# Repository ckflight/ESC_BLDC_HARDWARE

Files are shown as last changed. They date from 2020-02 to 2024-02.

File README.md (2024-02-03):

# BLHELI_S Electronic Speed Controller Hardware Design

#### ESC Information:

 * BLDC 3 phase motor speed controller hardware design working with open source BLHeli_S C configuration firmware C_H_30.

 * The ESC is tested on a real quadcopter with brushless motors at 40 Ampere current rating. 
 
 * TPN2R703NL Power MOSFETs are used on this design, which are capable of delivering current up to 45 Ampere for normal operation and 90 Ampere peak for short pulse.
 
 * MP1907 High Frequency Half Bridge Gate driver is used for controlling the Power MOSFETs. High power MOSFET transistors have high Q and capacitance values. To open the gate it requires high amount of current in short amount of time where current requirement decreases exponentially. This is the reason for using a Gate Driver. Also an extra gate resistor is populated at the input of MOSFET gate pin.
 
 $$ Igate(max) = {Vgate \over Rgate} $$

        4S Lipo Battery Vgate = 16V, Rgate = 10 Ohm and Igate(max) = 1.5A
 
 $$ Igate = {Qfet \over Tswitch} $$
 
         For a MOSFET with Qtotal = 50nC Tswtich = 500nS and Igate(needed) = 0.1A.
         Therefore, a 100 Ohm gate resistor is populated.

 * Phase C has current bar trace. Or it can be done with extra solder on the trace.

esc1

esc1

esc2

# BLHELI_S Firmware Flashing Guide

When esc is new assembled the EFM8BB2 does not have BLHeli_S Bootloader.
For the first time flashing, 4wire interface is used by using C2CK, C2D, 3.3v and GND pins where it will load both bootloader and firmware to esc.
After this step, esc can be flashed with 1-Wire interface (Esc's pwm pin).

####Flashing ESC for the first time.

1. Open "Make interfaces" section
2. Select the Arduino board that will be used as programmer.
3. Click "Arduino 4way-interface" and flash it to arduino.
   (Now arduino became a 4wire programmer)

4. Select "SILABS C2 (4way if)"
5. Connect Arduino to Custom ESC
       GND to GND 
       3.3v to 3.3v
       Arduino Pin12 to C2D 
       Arduino Pin11 to C2CK
6. Open ESC Setup section and connect to esc and click Flash BLHeli
   (choose suitable version, my custom quadcopter esc v2 is working with C type)

Now the esc is both flashed with blheli bootloader and the blheli firmware, 
therefore 1wire interface can be used which is the esc's pwm pin. 
Or flight controller can be used in passthrough mode.

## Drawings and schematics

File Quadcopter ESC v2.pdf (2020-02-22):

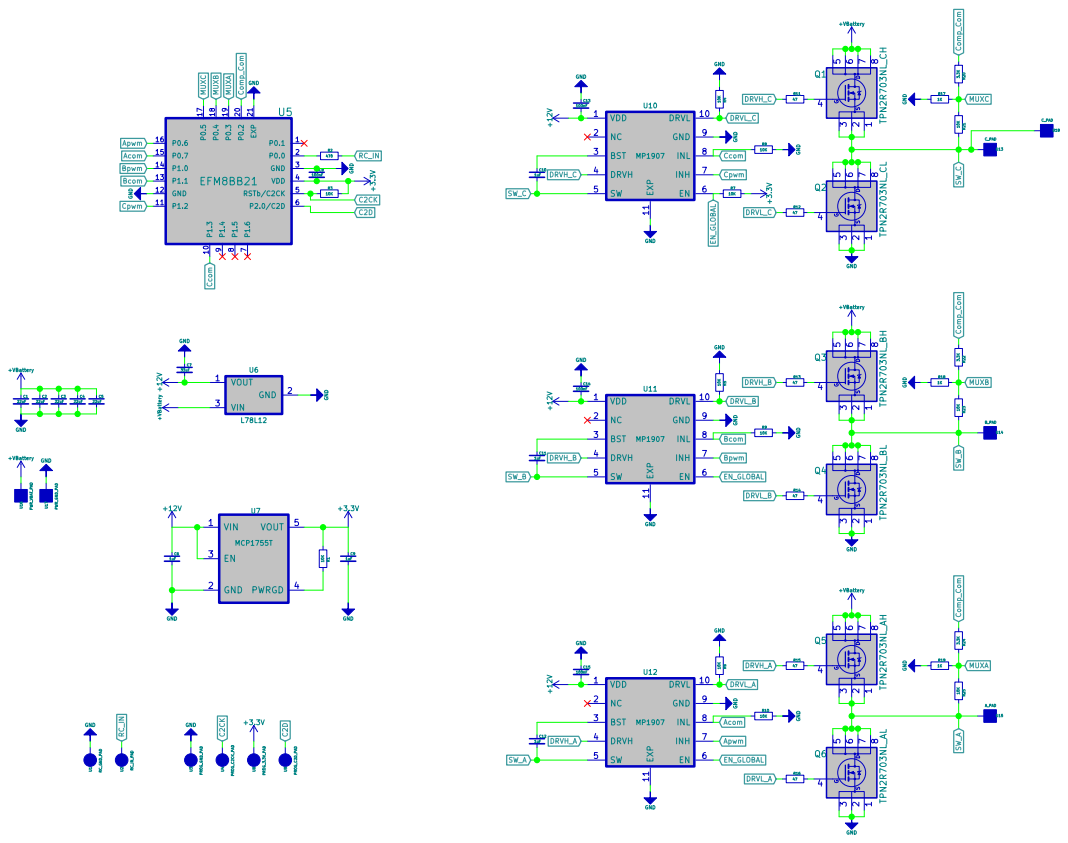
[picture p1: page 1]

File: Quadcopter ESC v2.sch Sheet: /
Id: 1/1 Title: Cenk Keskin

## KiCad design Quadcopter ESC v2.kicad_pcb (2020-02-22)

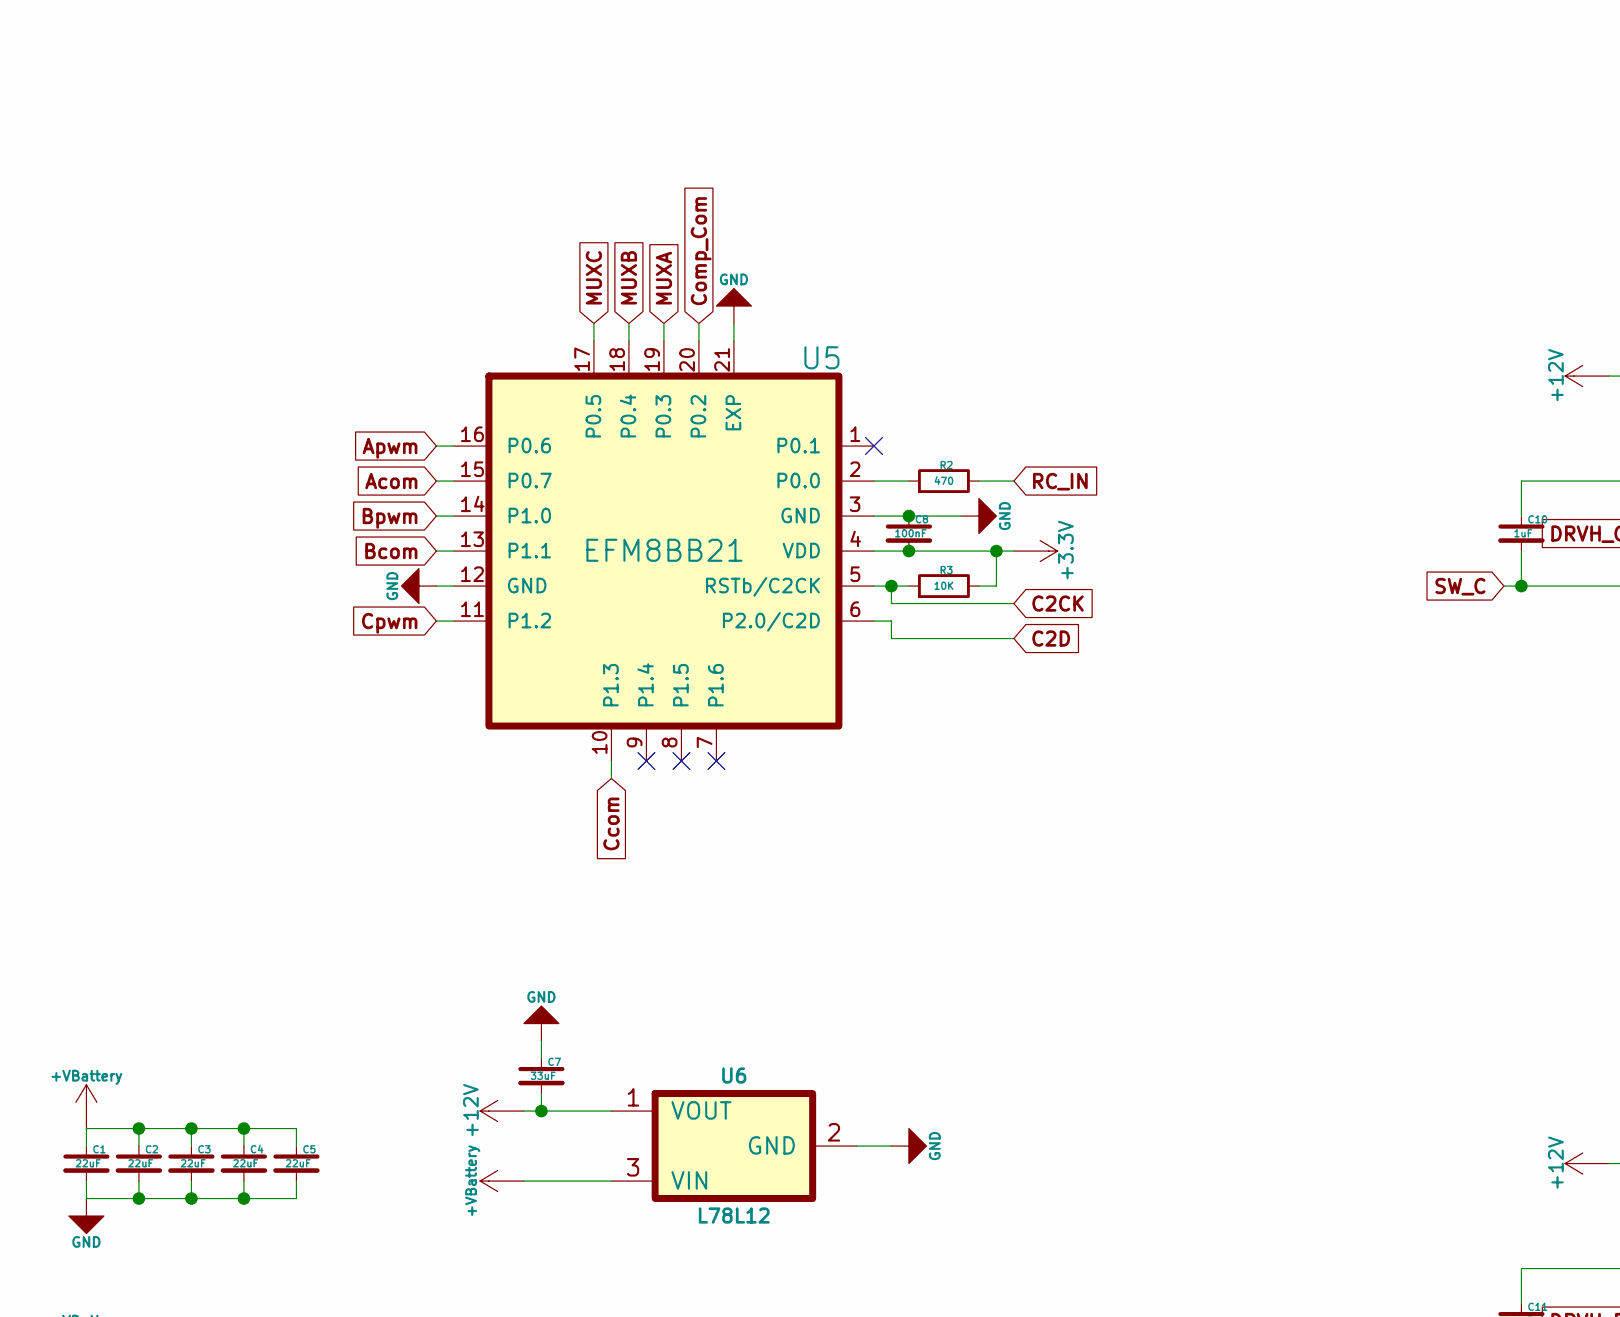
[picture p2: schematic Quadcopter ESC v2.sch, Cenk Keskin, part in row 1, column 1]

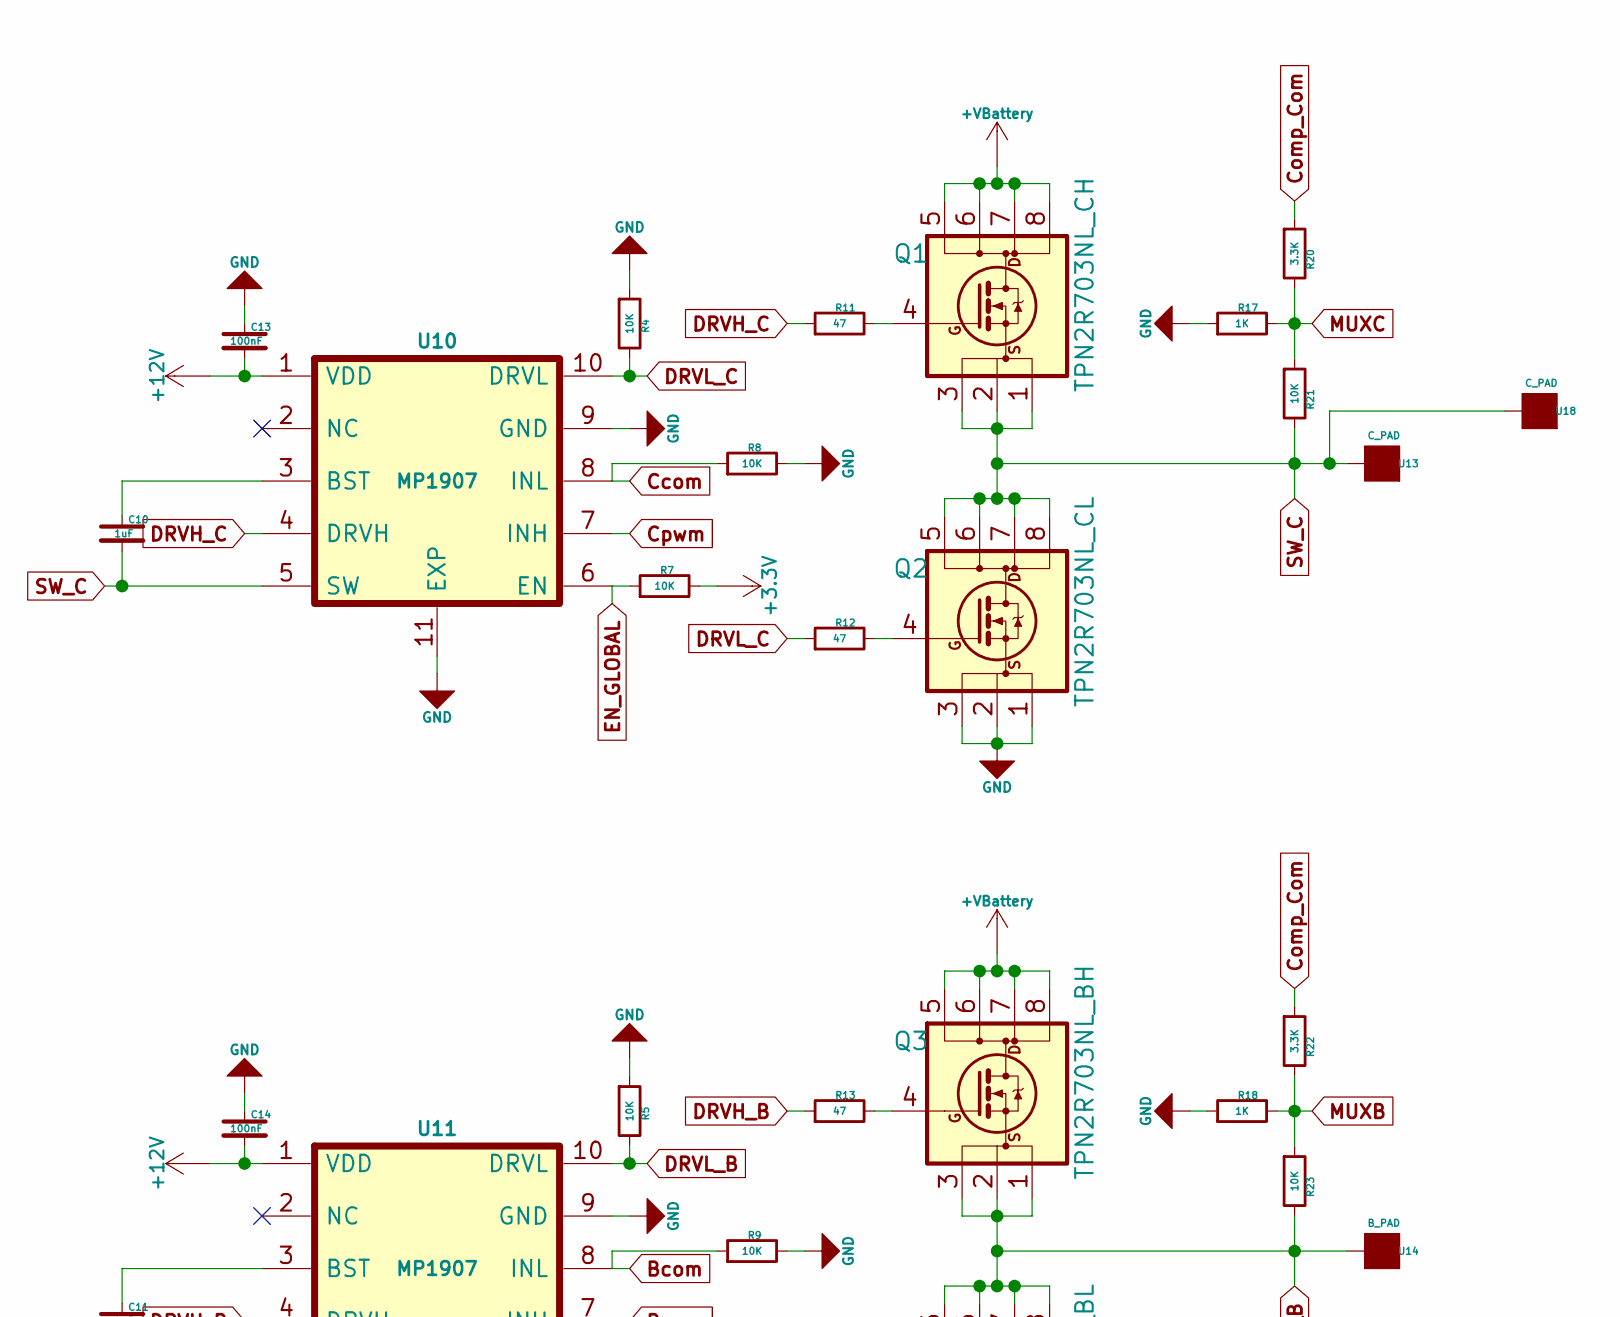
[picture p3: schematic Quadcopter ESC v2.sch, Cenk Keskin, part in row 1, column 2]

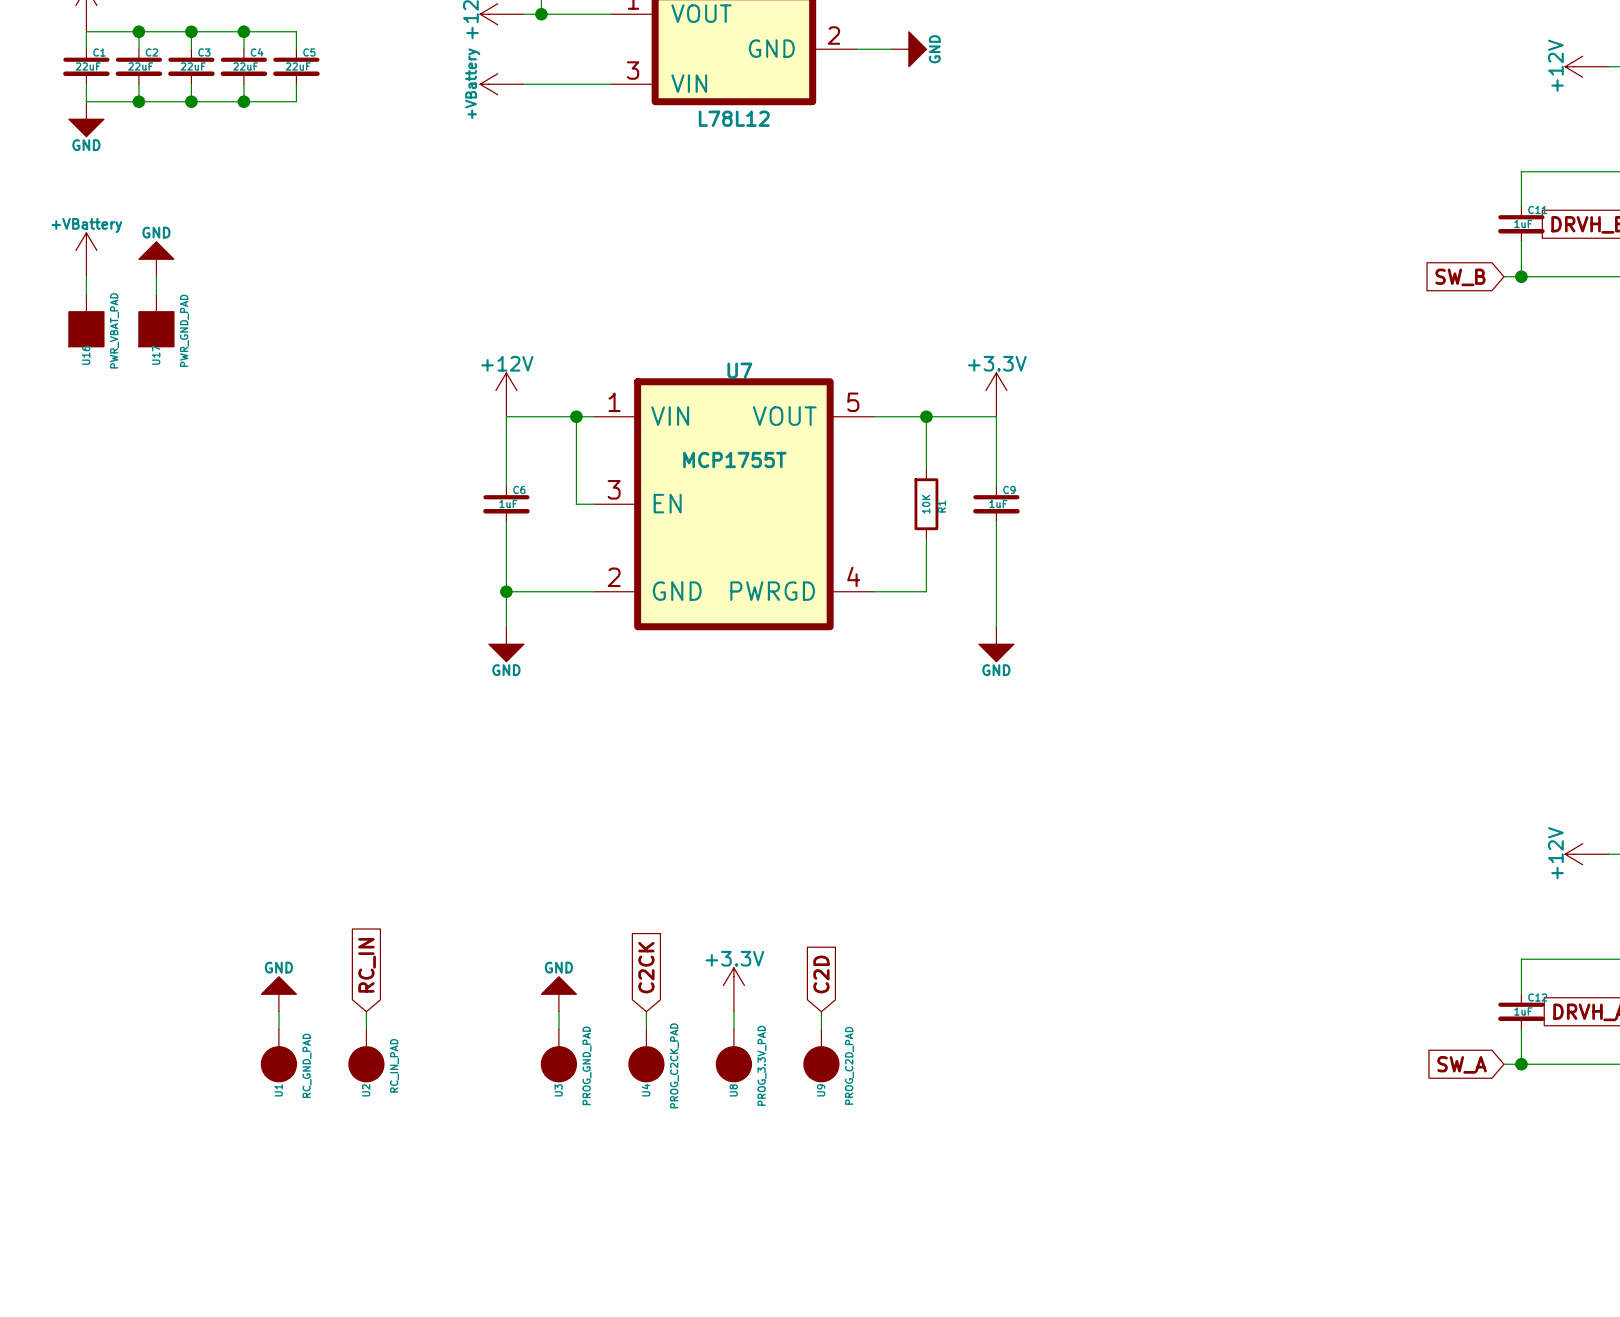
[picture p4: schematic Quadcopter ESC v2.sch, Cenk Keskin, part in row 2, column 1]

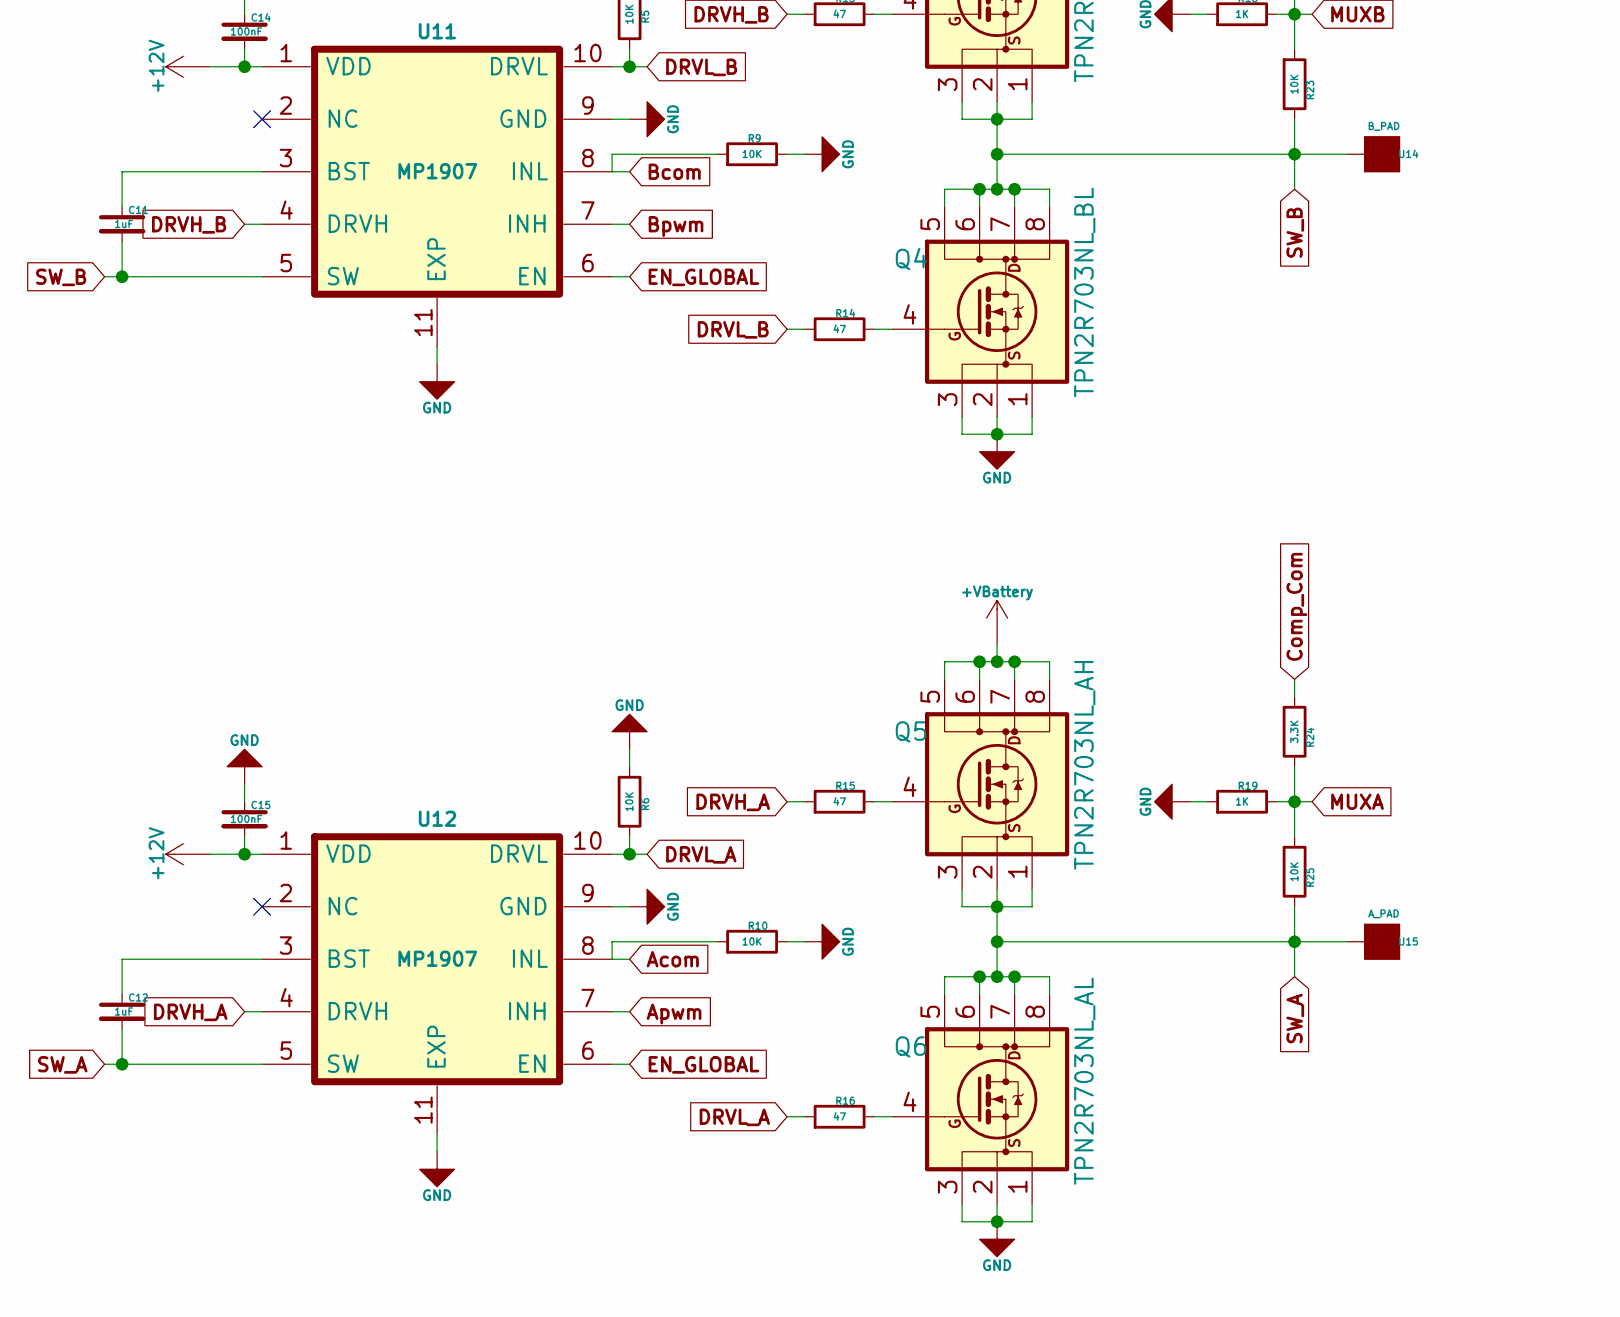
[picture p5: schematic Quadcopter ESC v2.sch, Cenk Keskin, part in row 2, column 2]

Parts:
C1, C2, C3, C4, C5: 22uF; SMD_0805
C6, C9, C10, C11, C12: 1uF; SMD_0603
C7: 33uF; SMD_1210
C8, C13, C14, C15: 100nF; SMD_0402
Q1: TPN2R703NL_CH; TSDSON_8
Q2: TPN2R703NL_CL; TSDSON_8
Q3: TPN2R703NL_BH; TSDSON_8
Q4: TPN2R703NL_BL; TSDSON_8
Q5: TPN2R703NL_AH; TSDSON_8
Q6: TPN2R703NL_AL; TSDSON_8
R1, R3, R4, R5, R6, R7, R8, R9, R10, R21, R23, R25: 10K; SMD_0402
R2: 470; SMD_0402
R11, R12, R13, R14, R15, R16: 47; SMD_0402
R17, R18, R19: 1K; SMD_0402
R20, R22, R24: 3.3K; SMD_0402
U1: RC_GND_PAD; SolderPad_1_2x2.5mm_SMD_Oval
U2: RC_IN_PAD; SolderPad_1_2x2.5mm_SMD_Oval
U3: PROG_GND_PAD; SolderPad_1_1.2mm_SMD_Circle
U4: PROG_C2CK_PAD; SolderPad_1_1.2mm_SMD_Circle
U5: EFM8BB21; QFN20_1EXP_3x3mm_Pitch0.5mm
U6: L78L12; SOT89-3
U7: MCP1755T; SOT23_5
U8: PROG_3.3V_PAD; SolderPad_1_1.2mm_SMD_Circle
U9: PROG_C2D_PAD; SolderPad_1_1.2mm_SMD_Circle
U10, U11, U12: MP1907; QFN10_1EXP_3x3mm_Pitch0.5mm
U13: C_PAD; SolderPad_1_2.5mm_SMD_Rectangle
U14: B_PAD; SolderPad_1_2.5mm_SMD_Rectangle
U15: A_PAD; SolderPad_1_2.5mm_SMD_Rectangle
U16: PWR_VBAT_PAD; SolderPad_1_2.5mm_SMD_Rectangle
U17: PWR_GND_PAD; SolderPad_1_2.5mm_SMD_Rectangle
U18: C_PAD; SolderPad_1_1x8mm_SMD_BUSBAR

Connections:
+3V3: C8.2, C9.1, R1.1, R3.2, R7.2, U5.4 (VDD), U7.5 (VOUT), U8.1
+12V: C6.1, C7.2, C13.2, C14.2, C15.2, U6.1 (VOUT), U7.1 (VIN), U7.3 (EN), U10.1 (VDD), U11.1 (VDD), U12.1 (VDD)
+VBattery: C1.1, C2.1, C3.1, C4.1, C5.1, Q1.5 (D), Q1.6 (D), Q1.7 (D), Q1.8 (D), Q3.5 (D), Q3.6 (D), Q3.7 (D), Q3.8 (D), Q5.5 (D), Q5.6 (D), Q5.7 (D), Q5.8 (D), U6.3 (VIN), U16.1
Acom: R10.1, U5.15 (P0.7), U12.8 (INL)
Apwm: U5.16 (P0.6), U12.7 (INH)
Bcom: R9.1, U5.13 (P1.1), U11.8 (INL)
Bpwm: U5.14 (P1.0), U11.7 (INH)
C2CK: R3.1, U4.1, U5.5 (RSTb/C2CK)
C2D: U5.6 (P2.0/C2D), U9.1
Ccom: R8.1, U5.10 (P1.3), U10.8 (INL)
Comp_Com: R20.1, R22.1, R24.1, U5.20 (P0.2)
Cpwm: U5.11 (P1.2), U10.7 (INH)
DRVH_A: R15.1, U12.4 (DRVH)
DRVH_B: R13.1, U11.4 (DRVH)
DRVH_C: R11.1, U10.4 (DRVH)
DRVL_A: R6.2, R16.1, U12.10 (DRVL)
DRVL_B: R5.2, R14.1, U11.10 (DRVL)
DRVL_C: R4.2, R12.1, U10.10 (DRVL)
EN_GLOBAL: R7.1, U10.6 (EN), U11.6 (EN), U12.6 (EN)
GND: C1.2, C2.2, C3.2, C4.2, C5.2, C6.2, C7.1, C8.1, C9.2, C13.1, C14.1, C15.1, Q2.1 (S), Q2.2 (S), Q2.3 (S), Q4.1 (S), Q4.2 (S), Q4.3 (S), Q6.1 (S), Q6.2 (S), Q6.3 (S), R4.1, R5.1, R6.1, R8.2, R9.2, R10.2, R17.1, R18.1, R19.1, U1.1, U3.1, U5.3 (GND), U5.12 (GND), U5.21 (EXP), U6.2 (GND), U7.2 (GND), U10.9 (GND), U10.11 (EXP), U11.9 (GND), U11.11 (EXP), U12.9 (GND), U12.11 (EXP), U17.1
MUXA: R19.2, R24.2, R25.1, U5.19 (P0.3)
MUXB: R18.2, R22.2, R23.1, U5.18 (P0.4)
MUXC: R17.2, R20.2, R21.1, U5.17 (P0.5)
unnamed: C10.1, U10.3 (BST)
unnamed: C11.1, U11.3 (BST)
unnamed: C12.1, U12.3 (BST)
unnamed: Q1.4 (G), R11.2
unnamed: Q2.4 (G), R12.2
unnamed: Q3.4 (G), R13.2
unnamed: Q4.4 (G), R14.2
unnamed: Q5.4 (G), R15.2
unnamed: Q6.4 (G), R16.2
unnamed: R1.2, U7.4 (PWRGD)
unnamed: R2.1, U5.2 (P0.0)
RC_IN: R2.2, U2.1
SW_A: C12.2, Q5.1 (S), Q5.2 (S), Q5.3 (S), Q6.5 (D), Q6.6 (D), Q6.7 (D), Q6.8 (D), R25.2, U12.5 (SW), U15.1
SW_B: C11.2, Q3.1 (S), Q3.2 (S), Q3.3 (S), Q4.5 (D), Q4.6 (D), Q4.7 (D), Q4.8 (D), R23.2, U11.5 (SW), U14.1
SW_C: C10.2, Q1.1 (S), Q1.2 (S), Q1.3 (S), Q2.5 (D), Q2.6 (D), Q2.7 (D), Q2.8 (D), R21.2, U10.5 (SW), U13.1, U18.1

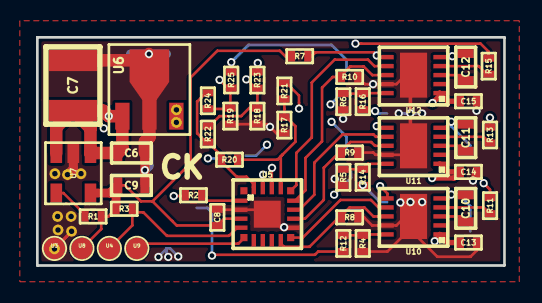
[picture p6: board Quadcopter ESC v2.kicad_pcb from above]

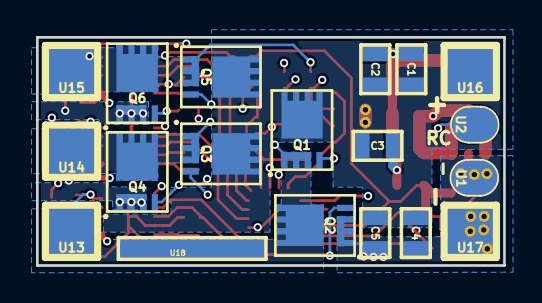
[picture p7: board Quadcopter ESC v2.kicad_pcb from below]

Board: 4 copper layers, 26.0 x 12.7 mm, 64 parts (19 on the bottom side), 38 nets.

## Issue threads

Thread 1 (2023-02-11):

Is there any info about the max Voltage this can handle?

MxFrs, 2023-02-11:

ckflight, 2023-02-11:
If you can check the schematic pdf file you will see that l78l12 regulator is used which is capable of handling input voltage up to 35 V volts.

catphish, 2023-05-06:
I believe the specified MOSFETs are rated for an absolute maximum of 30V Vds. This means that overall, as designed, the maximum practical voltage is going to be 30V. Given that this design is likely to be used to switch voltage from lithium batteries, and allowing a margin of safety, it looks like it should be good for up to 6S (25.2V at 100% SoC).

With regard to minimum voltage, if I'm understanding correctly, the driver requires an absolute minimum of 5.4V, and the 12V regulator has a dropout voltage of 1.7V, so the absolutely minimum operating voltage would be 7.1V. Again, assuming lithium batteries and a small margin of safety, this would equate to a minimum of 3S (9V at 0% SoC).

I hope you don't mind me resurrecting this thread. I thought it might be worth mentioning these conditions in the README.

Closed 2023-02-11.

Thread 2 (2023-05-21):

Motor not spinning properly

MxFrs, 2023-05-21:
Hello, I have rebuilt your design with some slightly different components to raise the maximum voltage. I managed to get the motor moving in an uncontrolled fashion. It looks like desync to me, but not really sure. I measured a lot of signals with an oscilloscope and for me all signals look pretty much fine, but as you can see in the video, it doesn't spin the motor. Did you ever experience something similar while developing/testing your design?
I've also attached my KiCad schemtic so you can maybe check weather I made any obvious mistakes (I tried to copy your design as much as possible).

https://github.com/ckflight/ESC_BLDC_HARDWARE/assets/35507432/e0968a6a-ea30-4bd2-8eca-dfb2842b4fb6

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

ckflight, 2023-05-22:
Hi with my design i did not experience anything like in the video. Its not
desync for sure though. It cannot commutate it seems like timing related
issue. I have check the transistor datasheet you used and its gate charge
and on off time is similar to the transistor in my design. I would suggest
changing the firmware timing try other ones like c h 20 25 etc.

Also pcb design is really important i made 4in1 esc with same setup and it
did not work properly. Meanwhile it was fine in 1 esc design.

Let me know if you figure it out the problem. I wonder what is the problem.

Regards.

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

MxFrs, 2023-05-22:
Thanks for the tips, I will try with the different firmware.
Also, I forgot to mention, that I am actually using different Mosfets (https://www.mouser.de/ProductDetail/?qs=gt1LBUVyoHmr9i%252B8H6gEPw%3D%3D). They have for example a higher gate charge. Can you specify what to look out for to check, weather the gates are driven properly? I guess I would want to see a kind of square signal on the gate pin which has high enough voltage?

ckflight, 2023-05-22:
Check description of the project there are 2 formulas. Simply transistor
with higher gate charge meaning more powerful, it needs higher current at
micro milli second level like from 2 3 ampere to 0 in millisecond to
properly drive the gate of the transistor.

Addition to the suggestions i said in thebprevious mail also decrease the
gate resistor value from 47 to something lower like 30 20 etc to drive with
higher current.

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

ckflight, 2023-05-22:
Long story short, The transistor you use is powerful and it has higher
switching time because it needs higher current to charge itself therefore
it takes time. Try firmware with higher delay than 30 also decrease gate
resistor value little bit. It should work because it is working but not
commutating properly roght now.

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

MxFrs, 2023-05-23:
I tried all the following firmwares with 47 Ohm resistors and, by adding the same in parallel, 23.5 Ohm. I tried C-H-30, 15, 5, 40, 50, 70 and 90. Unfortunately no real difference between all the versions. I also lowered the startup power to 0.125 which resulted in the motor starting slower and actually making about one revolution before starting to do weird stuff again. Any other ideas?

ckflight, 2023-05-23:
Then as i mentioned before, pcb design is important. When 2 of the motor
connection is connected third one is for feedback for detecting the phase
of the motor. Maybe that signal affected by return currents etc. Can you
compare your esc design's motor phases to a working esc.

Also can you change the transistors to a less powerfull one to cancel out
that option as well.

On Tue, 23 May 2023, 23:45 Maximilian Fries, ***@***.***>
wrote:

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

Npidys, 2023-06-11:
@MxFrs  Please check your gate driver's maximum source/sink current capabilities; they are not enough to drive the FETs in your design, assuming the fastest turn-on. It is possible to drive a FET slower with less current, (turn-on time is proportional to the gate current of the FET), but that has a lower limit because a second FET turn-on cycle might start before the first FET is wholly discharged, due to overlapping drive signals from the FC; this would create a shoot-through (electrical short between two phases of the 3-phase half bridge) and fault the ESC.

Closed 2024-02-02.

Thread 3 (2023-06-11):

Queries about development

Npidys, 2023-06-11:
I have a few queries about developing an ESC similar to this, as a part of a student project:

1. What was the battery voltage when you tested this ESC at 40A? Is it limited to 3S/4S ?
2. The MP1907 drivers are currently out of stock. Can they be replaced with MP1907A, in your opinion? The electrical quantities look mostly the same to me. https://www.monolithicpower.com/en/mp1907a.html - MP1907A

Thanks!

ckflight, 2023-09-22:
Hi,
1. It is tested with both 4s and 6s. Check the maximum ratings which is clarified here: https://github.com/ckflight/ESC_BLDC_HARDWARE/issues/1

2. Yes it looks exactly the same.

You are welcome. Regards.

Closed 2024-02-02.

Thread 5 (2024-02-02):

Firmware upload probelm

maniksingla2166, 2024-02-02:
Hi, i have a query,
I made a pcb using your schematic diagram. I am unable to upload the blheli_s firmware in it . Is there any special pin or any process i need to follow to upload the firmware ?
Currently i am using  BlheliSuite as the configurator for uploading the firmware.
It is not detecting my esc,  whereas it is detecting the other readymade esc which already has a firmware in it .

Closed 2024-02-02.

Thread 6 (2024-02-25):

ESC goes into calibration mode every time.

maniksingla2166, 2024-02-25:
Hiii,
we have some success in uploading the firmware but when i power the ESC and increasing the RC Stick it went to into calibration mode repetitive and motor is not spinning at all. Any help will be appreciated.

ckflight, 2024-02-25:
If it goes into the calibration mode then your rc is not calibrated. It send higher throttle command than the idle value. Try to increase idle value and test again. Also are you using my own design.

maniksingla2166, 2024-03-06:
Hi, sorry for the late reply , had my exams in between . Thanks for all the help , got it working , there were some minor issues in assembling the pcb .

Closed 2024-03-06.

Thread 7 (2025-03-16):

Gate drivers and mosfets

dstromeng, 2025-03-16:
Hi @ckflight
First of all, great project and thanks for sharing this.

I would like to know if you know of other options for gate drivers. I am trying to build this using SMT assembly service through JLPCB and weirdly they don't have this in stock.
I wanted to know if you may have tried some other gate drivers or had any recommendations.

Closed 2025-03-16.
